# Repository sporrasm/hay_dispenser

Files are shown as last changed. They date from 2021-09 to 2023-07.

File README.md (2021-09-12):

Readme for project horse_feeder

Remeber to run the export script from ESP install dir!

To configure (once per project), run

```
idf.py set-target esp32
idf.py menuconfig
```
Alternatively, WiFi SSID and password can be
set with `wifi_config.sh`. Place SSID and password
in `wifi_info.txt` in the following format:

```
SSID=YOUR_NETWORK_SSID
PASS=YOUR_PASSWORD
```
`wifi_info.txt` is automatically ignored in version
control and thus your password is safe.

To build, run
```
idf.py build
```
Finally, to flash and monitor, run

```
idf.py -p ESP_SERIAL_PORT flash monitor
```

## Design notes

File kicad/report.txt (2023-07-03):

Info: Processing symbol 'R17:Resistor_SMD:R_0805_2012Metric_Pad1.20x1.40mm_HandSolder'.
Info: Processing symbol 'R9:Resistor_SMD:R_0805_2012Metric_Pad1.20x1.40mm_HandSolder'.
Info: Processing symbol 'R10:Resistor_SMD:R_0805_2012Metric_Pad1.20x1.40mm_HandSolder'.
Info: Processing symbol 'R11:Resistor_SMD:R_0805_2012Metric_Pad1.20x1.40mm_HandSolder'.
Info: Processing symbol 'R12:Resistor_SMD:R_0805_2012Metric_Pad1.20x1.40mm_HandSolder'.
Info: Processing symbol 'C1:Capacitor_SMD:C_0805_2012Metric_Pad1.18x1.45mm_HandSolder'.
Info: Processing symbol 'R14:Resistor_SMD:R_0805_2012Metric_Pad1.20x1.40mm_HandSolder'.
Info: Processing symbol 'R15:Resistor_SMD:R_0805_2012Metric_Pad1.20x1.40mm_HandSolder'.
Info: Processing symbol 'R16:Resistor_SMD:R_0805_2012Metric_Pad1.20x1.40mm_HandSolder'.
Info: Processing symbol 'R8:Resistor_SMD:R_0805_2012Metric_Pad1.20x1.40mm_HandSolder'.
Info: Processing symbol 'R18:Resistor_SMD:R_0805_2012Metric_Pad1.20x1.40mm_HandSolder'.
Info: Processing symbol 'R19:Resistor_SMD:R_0805_2012Metric_Pad1.20x1.40mm_HandSolder'.
Info: Processing symbol 'R20:Resistor_SMD:R_0805_2012Metric_Pad1.20x1.40mm_HandSolder'.
Info: Processing symbol 'R21:Resistor_SMD:R_0805_2012Metric_Pad1.20x1.40mm_HandSolder'.
Info: Processing symbol 'R22:Resistor_SMD:R_0805_2012Metric_Pad1.20x1.40mm_HandSolder'.
Info: Processing symbol 'R23:Resistor_SMD:R_0805_2012Metric_Pad1.20x1.40mm_HandSolder'.
Info: Processing symbol 'R24:Resistor_SMD:R_0805_2012Metric_Pad1.20x1.40mm_HandSolder'.
Info: Processing symbol 'R25:Resistor_SMD:R_0805_2012Metric_Pad1.20x1.40mm_HandSolder'.
Info: Processing symbol 'R7:Resistor_SMD:R_0805_2012Metric_Pad1.20x1.40mm_HandSolder'.
Info: Processing symbol 'R6:Resistor_SMD:R_0805_2012Metric_Pad1.20x1.40mm_HandSolder'.
Info: Processing symbol 'R5:Resistor_SMD:R_0805_2012Metric_Pad1.20x1.40mm_HandSolder'.
Info: Processing symbol 'R4:Resistor_SMD:R_0805_2012Metric_Pad1.20x1.40mm_HandSolder'.
Info: Processing symbol 'R3:Resistor_SMD:R_0805_2012Metric_Pad1.20x1.40mm_HandSolder'.
Info: Processing symbol 'R2:Resistor_SMD:R_0805_2012Metric_Pad1.20x1.40mm_HandSolder'.
Info: Processing symbol 'R1:Resistor_SMD:R_0805_2012Metric_Pad1.20x1.40mm_HandSolder'.
Info: Processing symbol 'Q8:Package_TO_SOT_SMD:SOT-23'.
Info: Processing symbol 'Q7:Package_TO_SOT_SMD:SOT-23'.
Info: Processing symbol 'Q6:Package_TO_SOT_SMD:SOT-23'.
Info: Processing symbol 'Q5:Package_TO_SOT_SMD:SOT-23'.
Info: Processing symbol 'Q4:Package_TO_SOT_SMD:SOT-23'.
Info: Processing symbol 'Q3:Package_TO_SOT_SMD:SOT-23'.
Info: Processing symbol 'Q2:Package_TO_SOT_SMD:SOT-23'.
Info: Processing symbol 'Q1:Package_TO_SOT_SMD:SOT-23'.
Info: Processing symbol 'R41:Resistor_SMD:R_0805_2012Metric_Pad1.20x1.40mm_HandSolder'.
Info: Processing symbol 'U9:devkits:AMSROL-783'.
Info: Processing symbol 'U8:devkits:ESP32_DevkitC_ExtraPins'.
Info: Processing symbol 'U6:Package_SO:TSSOP-16_4.4x5mm_P0.65mm'.
Info: Processing symbol 'U5:Package_SO:TSSOP-16_4.4x5mm_P0.65mm'.
Info: Processing symbol 'U4:Package_SO:SOIC-8-1EP_3.9x4.9mm_P1.27mm_EP2.29x3mm'.
Info: Processing symbol 'U3:Package_SO:SOIC-8-1EP_3.9x4.9mm_P1.27mm_EP2.29x3mm'.
Info: Processing symbol 'U2:Package_SO:SOIC-8-1EP_3.9x4.9mm_P1.27mm_EP2.29x3mm'.
Info: Processing symbol 'U1:Package_SO:SOIC-8-1EP_3.9x4.9mm_P1.27mm_EP2.29x3mm'.
Info: Processing symbol 'SW5:Connector_TE-Connectivity:TE_826576-3_1x03_P3.96mm_Vertical'.
Info: Processing symbol 'SW4:Connector_PinHeader_2.54mm:PinHeader_1x02_P2.54mm_Vertical'.
Info: Processing symbol 'SW3:Connector_PinHeader_2.54mm:PinHeader_1x02_P2.54mm_Vertical'.
Info: Processing symbol 'SW2:Connector_PinHeader_2.54mm:PinHeader_1x02_P2.54mm_Vertical'.
Info: Processing symbol 'SW1:Connector_PinHeader_2.54mm:PinHeader_1x02_P2.54mm_Vertical'.
Info: Processing symbol 'Ropt1:Resistor_SMD:R_0805_2012Metric_Pad1.20x1.40mm_HandSolder'.
Info: Processing symbol 'R42:Resistor_SMD:R_0805_2012Metric_Pad1.20x1.40mm_HandSolder'.
Info: Processing symbol 'R13:Resistor_SMD:R_0805_2012Metric_Pad1.20x1.40mm_HandSolder'.
Info: Processing symbol 'R40:Resistor_SMD:R_0805_2012Metric_Pad1.20x1.40mm_HandSolder'.
Info: Processing symbol 'R39:Resistor_SMD:R_0805_2012Metric_Pad1.20x1.40mm_HandSolder'.
Info: Processing symbol 'R38:Resistor_SMD:R_0805_2012Metric_Pad1.20x1.40mm_HandSolder'.
Info: Processing symbol 'R37:Resistor_SMD:R_0805_2012Metric_Pad1.20x1.40mm_HandSolder'.
Info: Processing symbol 'R36:Resistor_SMD:R_0805_2012Metric_Pad1.20x1.40mm_HandSolder'.
Info: Processing symbol 'R35:Resistor_SMD:R_0805_2012Metric_Pad1.20x1.40mm_HandSolder'.
Info: Processing symbol 'R34:Resistor_SMD:R_0805_2012Metric_Pad1.20x1.40mm_HandSolder'.
Info: Processing symbol 'R33:Resistor_SMD:R_0805_2012Metric_Pad1.20x1.40mm_HandSolder'.
Info: Processing symbol 'R32:Resistor_SMD:R_0805_2012Metric_Pad1.20x1.40mm_HandSolder'.
Info: Processing symbol 'R31:Resistor_SMD:R_0805_2012Metric_Pad1.20x1.40mm_HandSolder'.
Info: Processing symbol 'R30:Resistor_SMD:R_0805_2012Metric_Pad1.20x1.40mm_HandSolder'.
Info: Processing symbol 'R29:Resistor_SMD:R_0805_2012Metric_Pad1.20x1.40mm_HandSolder'.
Info: Processing symbol 'R28:Resistor_SMD:R_0805_2012Metric_Pad1.20x1.40mm_HandSolder'.
Info: Processing symbol 'R27:Resistor_SMD:R_0805_2012Metric_Pad1.20x1.40mm_HandSolder'.
Info: Processing symbol 'R26:Resistor_SMD:R_0805_2012Metric_Pad1.20x1.40mm_HandSolder'.
Info: Processing symbol 'D1:Diode_SMD:D_SMB'.
Info: Processing symbol 'J7:Connector_PinHeader_2.54mm:PinHeader_2x02_P2.54mm_Vertical'.
Info: Processing symbol 'J6:Connector_PinHeader_2.54mm:PinHeader_2x02_P2.54mm_Vertical'.
Info: Processing symbol 'J5:Connector_PinHeader_2.54mm:PinHeader_2x02_P2.54mm_Vertical'.
Info: Processing symbol 'J4:Connector_PinHeader_2.54mm:PinHeader_2x02_P2.54mm_Vertical'.
Info: Processing symbol 'J3:Connector_PinHeader_2.54mm:PinHeader_2x02_P2.54mm_Vertical'.
Info: Processing symbol 'J2:Connector_PinHeader_2.54mm:PinHeader_2x02_P2.54mm_Vertical'.
Info: Processing symbol 'J1:Connector_PinHeader_2.54mm:PinHeader_2x02_P2.54mm_Vertical'.
Info: Processing symbol 'D8:Diode_SMD:D_SMB'.
Info: Processing symbol 'D7:Diode_SMD:D_SMB'.
Info: Processing symbol 'D6:Diode_SMD:D_SMB'.
Info: Processing symbol 'D5:Diode_SMD:D_SMB'.
Info: Processing symbol 'D4:Diode_SMD:D_SMB'.
Info: Processing symbol 'D3:Diode_SMD:D_SMB'.
Info: Processing symbol 'D2:Diode_SMD:D_SMB'.
Info: Processing symbol 'L2:Inductor_THT:L_Radial_D7.0mm_P3.00mm'.
Info: Processing symbol 'C14:Capacitor_THT:CP_Radial_D5.0mm_P2.50mm'.
Info: Processing symbol 'C13:Capacitor_THT:CP_Radial_D5.0mm_P2.50mm'.
Info: Processing symbol 'C12:Capacitor_THT:CP_Radial_D8.0mm_P3.50mm'.
Info: Processing symbol 'C11:Capacitor_THT:CP_Radial_D5.0mm_P2.50mm'.
Info: Processing symbol 'C10:Capacitor_THT:CP_Radial_D5.0mm_P2.50mm'.
Info: Processing symbol 'C9:Capacitor_THT:CP_Radial_D8.0mm_P3.50mm'.
Info: Processing symbol 'C8:Capacitor_SMD:C_0805_2012Metric_Pad1.18x1.45mm_HandSolder'.
Info: Processing symbol 'C7:Capacitor_SMD:C_0805_2012Metric_Pad1.18x1.45mm_HandSolder'.
Info: Processing symbol 'C6:Capacitor_SMD:C_0805_2012Metric_Pad1.18x1.45mm_HandSolder'.
Info: Processing symbol 'C5:Capacitor_SMD:C_0805_2012Metric_Pad1.18x1.45mm_HandSolder'.
Info: Processing symbol 'C4:Capacitor_SMD:C_0805_2012Metric_Pad1.18x1.45mm_HandSolder'.
Info: Processing symbol 'C3:Capacitor_SMD:C_0805_2012Metric_Pad1.18x1.45mm_HandSolder'.
Info: Processing symbol 'C2:Capacitor_SMD:C_0805_2012Metric_Pad1.18x1.45mm_HandSolder'.
Info: Processing symbol 'L3:Inductor_THT:L_Radial_D7.0mm_P3.00mm'.
Info: Processing symbol 'L1:Inductor_THT:L_Radial_D7.0mm_P3.00mm'.
Info: Processing symbol 'J9:Connector_Phoenix_MSTB:PhoenixContact_MSTBA_2,5_2-G_1x02_P5.00mm_Horizontal'.
Info: Processing symbol 'J10:Connector_PinHeader_2.00mm:PinHeader_1x04_P2.00mm_Vertical'.
Info: Processing symbol 'J8:Connector_PinHeader_2.54mm:PinHeader_2x02_P2.54mm_Vertical'.
Updated D5 symbol association from /00000000-0000-0000-0000-000061ebca90/00000000-0000-0000-0000-000061f9a212 to /00000000-0000-0000-0000-000061ebca90/12310255-a125-40a2-8815-03da1e133a0b.
Reconnected Q5 pin 1 from Net-(Q1-G) to Net-(Q5-G).
Reconnected J8 pin 4 from /IOs/LOCK_DET1 to /IOs/LOCK_DET7.
Reconnected D4 pin 2 from Net-(D2-A) to Net-(D4-A).
Updated D4 symbol association from /00000000-0000-0000-0000-000061ebca90/1fadecef-52da-4aaa-b496-044390b111f7 to /00000000-0000-0000-0000-000061ebca90/f83071ec-e386-489c-af28-ea3d26ad8b88.
Reconnected Q6 pin 3 from Net-(D2-A) to Net-(D6-A).
Reconnected D3 pin 2 from Net-(D1-A) to Net-(D3-A).
Updated D3 symbol association from /00000000-0000-0000-0000-000061ebca90/00000000-0000-0000-0000-000061f9a212 to /00000000-0000-0000-0000-000061ebca90/ba43a25b-48b8-4457-9719-1656a0430705.
Reconnected Q6 pin 1 from Net-(Q2-G) to Net-(Q6-G).
Updated Q6 symbol association from /00000000-0000-0000-0000-000061ebca90/9a64ff62-3964-40c4-85d5-2005a53f7bb7 to /00000000-0000-0000-0000-000061ebca90/19cce44a-ca22-4e9a-8f8b-97bd614c21f1.
Reconnected J8 pin 3 from Net-(D2-A) to Net-(D8-A).
Reconnected Q5 pin 3 from Net-(D1-A) to Net-(D5-A).
Updated R29 symbol association from /00000000-0000-0000-0000-000061ebca90/00000000-0000-0000-0000-000061f8473e to /00000000-0000-0000-0000-000061ebca90/3bc0eca3-92dc-4e1d-8b31-45b180863d8f.
Reconnected D5 pin 2 from Net-(D1-A) to Net-(D5-A).
Reconnected R32 pin 1 from /IOs/LOCK_EN0 to /IOs/LOCK_EN6.
Reconnected R32 pin 2 from Net-(U1-ENB) to Net-(U4-ENB).
Updated R32 symbol association from /00000000-0000-0000-0000-000061ebca90/00000000-0000-0000-0000-000061f84748 to /00000000-0000-0000-0000-000061ebca90/12d70f20-32db-4ce9-8402-37e04de7cd11.
Updated Q7 symbol association from /00000000-0000-0000-0000-000061ebca90/00000000-0000-0000-0000-000061f9a22a to /00000000-0000-0000-0000-000061ebca90/117ebf1d-a23b-43cb-92d2-cf0df6883d6a.
Reconnected R31 pin 1 from Net-(U1-ENA) to Net-(U4-ENA).
Reconnected R31 pin 2 from /IOs/LOCK_EN1 to /IOs/LOCK_EN7.
Updated R31 symbol association from /00000000-0000-0000-0000-000061ebca90/00000000-0000-0000-0000-000061f8473e to /00000000-0000-0000-0000-000061ebca90/c096ada7-25bf-42d8-b60a-c3b1d2fc6672.
Updated D6 symbol association from /00000000-0000-0000-0000-000061ebca90/1fadecef-52da-4aaa-b496-044390b111f7 to /00000000-0000-0000-0000-000061ebca90/009bf2af-9f41-490d-a20b-dce77ff50deb.
Reconnected R30 pin 2 from Net-(U1-ENB) to Net-(U3-ENB).
Reconnected R30 pin 1 from /IOs/LOCK_EN0 to /IOs/LOCK_EN4.
Updated R30 symbol association from /00000000-0000-0000-0000-000061ebca90/00000000-0000-0000-0000-000061f84748 to /00000000-0000-0000-0000-000061ebca90/f51487ca-ee80-4a78-abcf-102a507cea02.
Reconnected D6 pin 2 from Net-(D2-A) to Net-(D6-A).
Reconnected R29 pin 2 from /IOs/LOCK_EN1 to /IOs/LOCK_EN5.
Reconnected R29 pin 1 from Net-(U1-ENA) to Net-(U3-ENA).
Reconnected J7 pin 4 from /IOs/LOCK_DET0 to /IOs/LOCK_DET6.
Reconnected U3 pin 4 from /IOs/LOCK_IN1 to /IOs/LOCK_IN5.
Updated Q3 symbol association from /00000000-0000-0000-0000-000061ebca90/00000000-0000-0000-0000-000061f9a22a to /00000000-0000-0000-0000-000061ebca90/dab6c745-e6cc-45fe-9a9b-13cf7740417a.
Reconnected Q3 pin 1 from Net-(Q1-G) to Net-(Q3-G).
Reconnected U4 pin 1 from Net-(U1-ENA) to Net-(U4-ENA).
Reconnected U4 pin 2 from /IOs/LOCK_IN0 to /IOs/LOCK_IN6.
Reconnected U4 pin 4 from /IOs/LOCK_IN1 to /IOs/LOCK_IN7.
Reconnected U4 pin 5 from /IOs/LOCK1 to /IOs/LOCK7.
Reconnected U4 pin 7 from /IOs/LOCK0 to /IOs/LOCK6.
Reconnected U4 pin 8 from Net-(U1-ENB) to Net-(U4-ENB).
Updated U4 symbol association from /00000000-0000-0000-0000-000061ebca90/00000000-0000-0000-0000-000061fc2397 to /00000000-0000-0000-0000-000061ebca90/329a1e8b-e309-4d9a-a68a-94c8a32ff173.
Reconnected Q3 pin 3 from Net-(D1-A) to Net-(D3-A).
Reconnected U3 pin 8 from Net-(U1-ENB) to Net-(U3-ENB).
Reconnected U3 pin 7 from /IOs/LOCK0 to /IOs/LOCK4.
Reconnected U3 pin 5 from /IOs/LOCK1 to /IOs/LOCK5.
Updated Q5 symbol association from /00000000-0000-0000-0000-000061ebca90/00000000-0000-0000-0000-000061f9a22a to /00000000-0000-0000-0000-000061ebca90/90347d65-daa5-4414-a60e-72c4a4d0bfb0.
Reconnected U3 pin 2 from /IOs/LOCK_IN0 to /IOs/LOCK_IN4.
Reconnected U3 pin 1 from Net-(U1-ENA) to Net-(U3-ENA).
Updated U3 symbol association from /00000000-0000-0000-0000-000061ebca90/00000000-0000-0000-0000-000061fc2397 to /00000000-0000-0000-0000-000061ebca90/f14f373f-7c34-4b97-81f3-ad92c1f3f635.
Reconnected U2 pin 8 from Net-(U1-ENB) to Net-(U2-ENB).
Reconnected U2 pin 7 from /IOs/LOCK0 to /IOs/LOCK2.
Reconnected U2 pin 5 from /IOs/LOCK1 to /IOs/LOCK3.
Reconnected U2 pin 4 from /IOs/LOCK_IN1 to /IOs/LOCK_IN3.
Reconnected U2 pin 2 from /IOs/LOCK_IN0 to /IOs/LOCK_IN2.
Reconnected U2 pin 1 from Net-(U1-ENA) to Net-(U2-ENA).
Updated U2 symbol association from /00000000-0000-0000-0000-000061ebca90/00000000-0000-0000-0000-000061fc2397 to /00000000-0000-0000-0000-000061ebca90/1f8c6d32-524a-4a61-9146-b464a2e4b00f.
Updated Q4 symbol association from /00000000-0000-0000-0000-000061ebca90/9a64ff62-3964-40c4-85d5-2005a53f7bb7 to /00000000-0000-0000-0000-000061ebca90/2e4807ac-fbeb-4c4a-b1f8-ade59b8256ed.
Reconnected Q4 pin 1 from Net-(Q2-G) to Net-(Q4-G).
Reconnected Q4 pin 3 from Net-(D2-A) to Net-(D4-A).
Reconnected R10 pin 2 from /IOs/LOCK1 to /IOs/LOCK3.
Reconnected R15 pin 1 from /IOs/LOCK_DET0 to /IOs/LOCK_DET4.
Updated R15 symbol association from /00000000-0000-0000-0000-000061ebca90/00000000-0000-0000-0000-000061f9a118 to /00000000-0000-0000-0000-000061ebca90/5d248cbb-a3ee-4746-98de-e42f1b14ef73.
Reconnected J4 pin 3 from Net-(D2-A) to Net-(D4-A).
Reconnected R14 pin 1 from Net-(Q1-G) to Net-(Q5-G).
Updated R14 symbol association from /00000000-0000-0000-0000-000061ebca90/00000000-0000-0000-0000-000061f9a127 to /00000000-0000-0000-0000-000061ebca90/5689a1f5-9090-4234-bba9-7dff9da78761.
Reconnected Q7 pin 3 from Net-(D1-A) to Net-(D7-A).
Reconnected R13 pin 1 from Net-(Q1-G) to Net-(Q5-G).
Reconnected R13 pin 2 from /IOs/LOCK0 to /IOs/LOCK4.
Updated R13 symbol association from /00000000-0000-0000-0000-000061ebca90/00000000-0000-0000-0000-000061f9a12d to /00000000-0000-0000-0000-000061ebca90/e7271d92-2a59-4a4c-9ece-0f144f666454.
Reconnected R12 pin 1 from /IOs/LOCK_DET1 to /IOs/LOCK_DET3.
Updated R12 symbol association from /00000000-0000-0000-0000-000061ebca90/acf82a41-7d0e-472a-a831-509c7dad960c to /00000000-0000-0000-0000-000061ebca90/bc75ee53-f973-43e8-9b8a-a9dcb3717276.
Updated J5 symbol association from /00000000-0000-0000-0000-000061ebca90/00000000-0000-0000-0000-000061f9a109 to /00000000-0000-0000-0000-000061ebca90/01534e29-1c65-493a-a183-ee503e500c0f.
Reconnected R11 pin 1 from Net-(Q2-G) to Net-(Q4-G).
Updated R11 symbol association from /00000000-0000-0000-0000-000061ebca90/e005b53f-12e7-4917-b024-14621842eea1 to /00000000-0000-0000-0000-000061ebca90/f1c19577-37a0-416f-b9f6-60572b592bf5.
Reconnected J5 pin 3 from Net-(D1-A) to Net-(D5-A).
Reconnected J4 pin 4 from /IOs/LOCK_DET1 to /IOs/LOCK_DET3.
Reconnected R10 pin 1 from Net-(Q2-G) to Net-(Q4-G).
Updated R10 symbol association from /00000000-0000-0000-0000-000061ebca90/a2109c77-97ea-4bdb-9450-69fe4743dba1 to /00000000-0000-0000-0000-000061ebca90/110e5a1b-0579-4342-8a50-bc9ee74117f4.
Reconnected J5 pin 4 from /IOs/LOCK_DET0 to /IOs/LOCK_DET4.
Reconnected R9 pin 1 from /IOs/LOCK_DET0 to /IOs/LOCK_DET2.
Updated R9 symbol association from /00000000-0000-0000-0000-000061ebca90/00000000-0000-0000-0000-000061f9a118 to /00000000-0000-0000-0000-000061ebca90/a2a08252-e1a3-4e8e-a624-c2db73924c49.
Reconnected J7 pin 3 from Net-(D1-A) to Net-(D7-A).
Reconnected R8 pin 1 from Net-(Q1-G) to Net-(Q3-G).
Updated R8 symbol association from /00000000-0000-0000-0000-000061ebca90/00000000-0000-0000-0000-000061f9a127 to /00000000-0000-0000-0000-000061ebca90/5699d61c-54a2-4d67-a252-4f0f22aa03cb.
Updated J6 symbol association from /00000000-0000-0000-0000-000061ebca90/d37b7b18-48a2-43dd-b725-8d8200de3ad7 to /00000000-0000-0000-0000-000061ebca90/7799ac4f-bc16-4e58-80f5-ee678a479432.
Reconnected R7 pin 1 from Net-(Q1-G) to Net-(Q3-G).
Reconnected R7 pin 2 from /IOs/LOCK0 to /IOs/LOCK2.
Updated R7 symbol association from /00000000-0000-0000-0000-000061ebca90/00000000-0000-0000-0000-000061f9a12d to /00000000-0000-0000-0000-000061ebca90/1e97676b-6e90-4e2b-9f52-2bc77df03034.
Reconnected J6 pin 3 from Net-(D2-A) to Net-(D6-A).
Reconnected J6 pin 4 from /IOs/LOCK_DET1 to /IOs/LOCK_DET5.
Updated J7 symbol association from /00000000-0000-0000-0000-000061ebca90/00000000-0000-0000-0000-000061f9a109 to /00000000-0000-0000-0000-000061ebca90/1b84dabf-0c1a-4e32-9baa-dc91dcef677a.
Updated J8 symbol association from /00000000-0000-0000-0000-000061ebca90/d37b7b18-48a2-43dd-b725-8d8200de3ad7 to /00000000-0000-0000-0000-000061ebca90/7a27e839-1899-4622-9983-cdac9ac2dc0d.
Reconnected R28 pin 1 from /IOs/LOCK_EN0 to /IOs/LOCK_EN2.
Updated R28 symbol association from /00000000-0000-0000-0000-000061ebca90/00000000-0000-0000-0000-000061f84748 to /00000000-0000-0000-0000-000061ebca90/9e823606-f83d-4ab2-8a34-e646199f153e.
Updated D7 symbol association from /00000000-0000-0000-0000-000061ebca90/00000000-0000-0000-0000-000061f9a212 to /00000000-0000-0000-0000-000061ebca90/b1030530-6fb9-4591-98a9-0427e75660df.
Reconnected R27 pin 2 from /IOs/LOCK_EN1 to /IOs/LOCK_EN3.
Reconnected R27 pin 1 from Net-(U1-ENA) to Net-(U2-ENA).
Updated R27 symbol association from /00000000-0000-0000-0000-000061ebca90/00000000-0000-0000-0000-000061f8473e to /00000000-0000-0000-0000-000061ebca90/26a5f1ab-7ebe-4985-b59a-fd3232592324.
Reconnected D7 pin 2 from Net-(D1-A) to Net-(D7-A).
Reconnected R28 pin 2 from Net-(U1-ENB) to Net-(U2-ENB).
Reconnected Q7 pin 1 from Net-(Q1-G) to Net-(Q7-G).
Updated D8 symbol association from /00000000-0000-0000-0000-000061ebca90/1fadecef-52da-4aaa-b496-044390b111f7 to /00000000-0000-0000-0000-000061ebca90/9ebdfd22-79c4-4adf-85de-91e1239ecd49.
Reconnected D8 pin 2 from Net-(D2-A) to Net-(D8-A).
Updated Q8 symbol association from /00000000-0000-0000-0000-000061ebca90/9a64ff62-3964-40c4-85d5-2005a53f7bb7 to /00000000-0000-0000-0000-000061ebca90/89a83a01-4313-41c3-ab5b-a217104dbb12.
Reconnected Q8 pin 3 from Net-(D2-A) to Net-(D8-A).
Updated J4 symbol association from /00000000-0000-0000-0000-000061ebca90/d37b7b18-48a2-43dd-b725-8d8200de3ad7 to /00000000-0000-0000-0000-000061ebca90/230b0a54-814c-4633-86d4-6288c8a4b25b.
Reconnected R17 pin 1 from Net-(Q2-G) to Net-(Q6-G).
Updated R16 symbol association from /00000000-0000-0000-0000-000061ebca90/a2109c77-97ea-4bdb-9450-69fe4743dba1 to /00000000-0000-0000-0000-000061ebca90/7600460e-baca-4eef-a013-d1cb4ffcadad.
Reconnected R16 pin 1 from Net-(Q2-G) to Net-(Q6-G).
Reconnected R16 pin 2 from /IOs/LOCK1 to /IOs/LOCK5.
Reconnected Q8 pin 1 from Net-(Q2-G) to Net-(Q8-G).
Updated R17 symbol association from /00000000-0000-0000-0000-000061ebca90/e005b53f-12e7-4917-b024-14621842eea1 to /00000000-0000-0000-0000-000061ebca90/eb4bc25c-40cd-4988-a59e-3364879d56c7.
Reconnected J3 pin 4 from /IOs/LOCK_DET0 to /IOs/LOCK_DET2.
Updated R18 symbol association from /00000000-0000-0000-0000-000061ebca90/acf82a41-7d0e-472a-a831-509c7dad960c to /00000000-0000-0000-0000-000061ebca90/407302c0-80a5-49a3-b481-c82105730bca.
Reconnected R18 pin 1 from /IOs/LOCK_DET1 to /IOs/LOCK_DET5.
Reconnected J3 pin 3 from Net-(D1-A) to Net-(D3-A).
Updated J3 symbol association from /00000000-0000-0000-0000-000061ebca90/00000000-0000-0000-0000-000061f9a109 to /00000000-0000-0000-0000-000061ebca90/5bc772af-2207-48a7-a277-9bfb6a1bbd47.
Warning: No net found for symbol U8 pin 40.
Warning: No net found for symbol U2 pin 9.
Warning: No net found for symbol U5 pin 10.
Warning: No net found for symbol U4 pin 9.
Warning: No net found for symbol U8 pin 39.
Warning: No net found for symbol U6 pin 10.
Warning: No net found for symbol U1 pin 9.
Warning: No net found for symbol U4 pin 9.
Warning: No net found for symbol U2 pin 9.
Warning: No net found for symbol U3 pin 9.
Warning: No net found for symbol U3 pin 9.
Error: Multiple footprints found for 'R29'.
Error: Multiple footprints found for 'R28'.
Error: Multiple footprints found for 'U4'.
Error: Multiple footprints found for 'R27'.
Error: Multiple footprints found for 'R30'.
Error: Multiple footprints found for 'U3'.
Error: Multiple footprints found for 'R31'.
Error: Multiple footprints found for 'R32'.
Error: Multiple footprints found for 'U2'.

Info: Total warnings: 11, errors: 9.

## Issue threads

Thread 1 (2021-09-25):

Timer fires too soon if alarm time is large

sporrasm, 2021-09-25:

sporrasm, 2021-09-25:
The timer seems to fire too soon provided that the value to be set is too large. This may be due to the fact the the timer alarm value is given in TIMER_SCALE units, which is equal to APB_CLOCK / CLOCK_DIV. Need to perform check whether the integer overflows and causes this.

sporrasm, 2021-09-25:
Fixed by a65deb02. Seems to be that I forgot to cast the input time in seconds to uint64_t, causing the alarm time value to be garbage. Hence, timer was acting erratically.

Closed 2021-09-25.

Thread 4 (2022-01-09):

Triggering locks after power down

sporrasm, 2022-01-09:
If power down happens during the feeding routine, the next lock corresponding to the next time stamp is released. This may cause issues if one of the plates has not triggered during the power down. Solution is to pulse all locks that are before the next lock to be pulsed (or monitor lock state via hardware)

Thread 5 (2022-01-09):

Timezone settings

sporrasm, 2022-01-09:
Timer is off by one hour during DST. Need to fix this at some point

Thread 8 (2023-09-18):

Change pin order of I2C io expanders

sporrasm, 2023-09-18:
The pin order in PCB rev 1.2 is a bit wonky for the I2C expanders. Could worth to change them to correct order so that lock index 0 truly corresponds to index 0 etc.

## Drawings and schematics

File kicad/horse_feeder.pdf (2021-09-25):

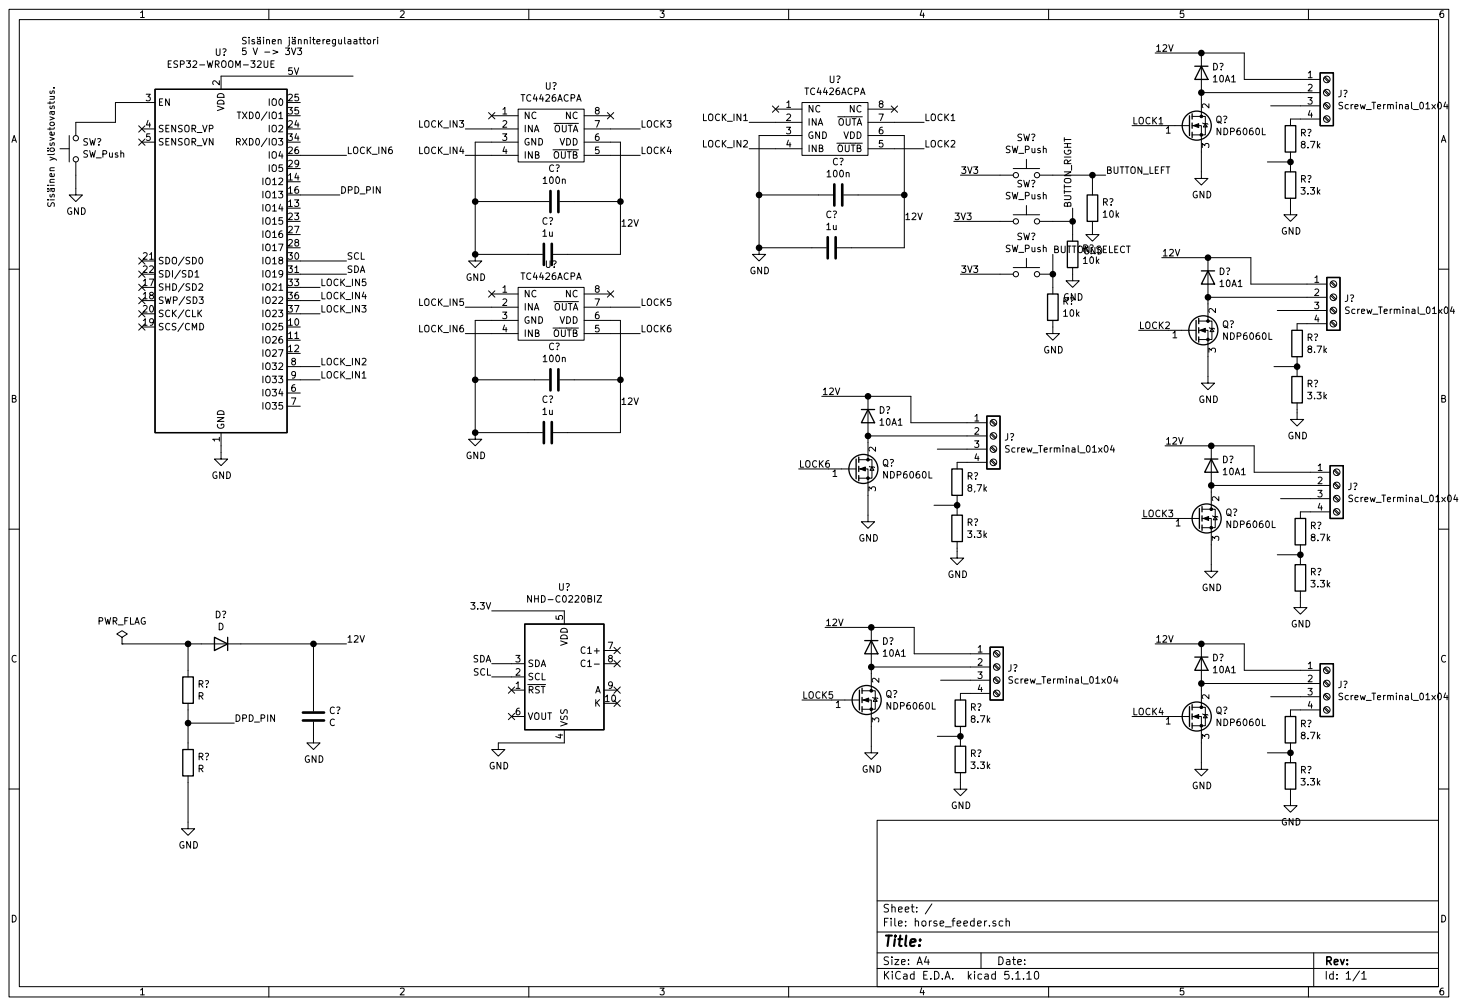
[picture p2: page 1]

LOCK1 Sisäinen jänniteregulaattori 5 V -> 3V3 Sisäinen ylösvetovastus.

2 SCK/CLK 20 SDO/SD0 21 SDI/SD1 22

File: horse_feeder.sch Sheet: / GND

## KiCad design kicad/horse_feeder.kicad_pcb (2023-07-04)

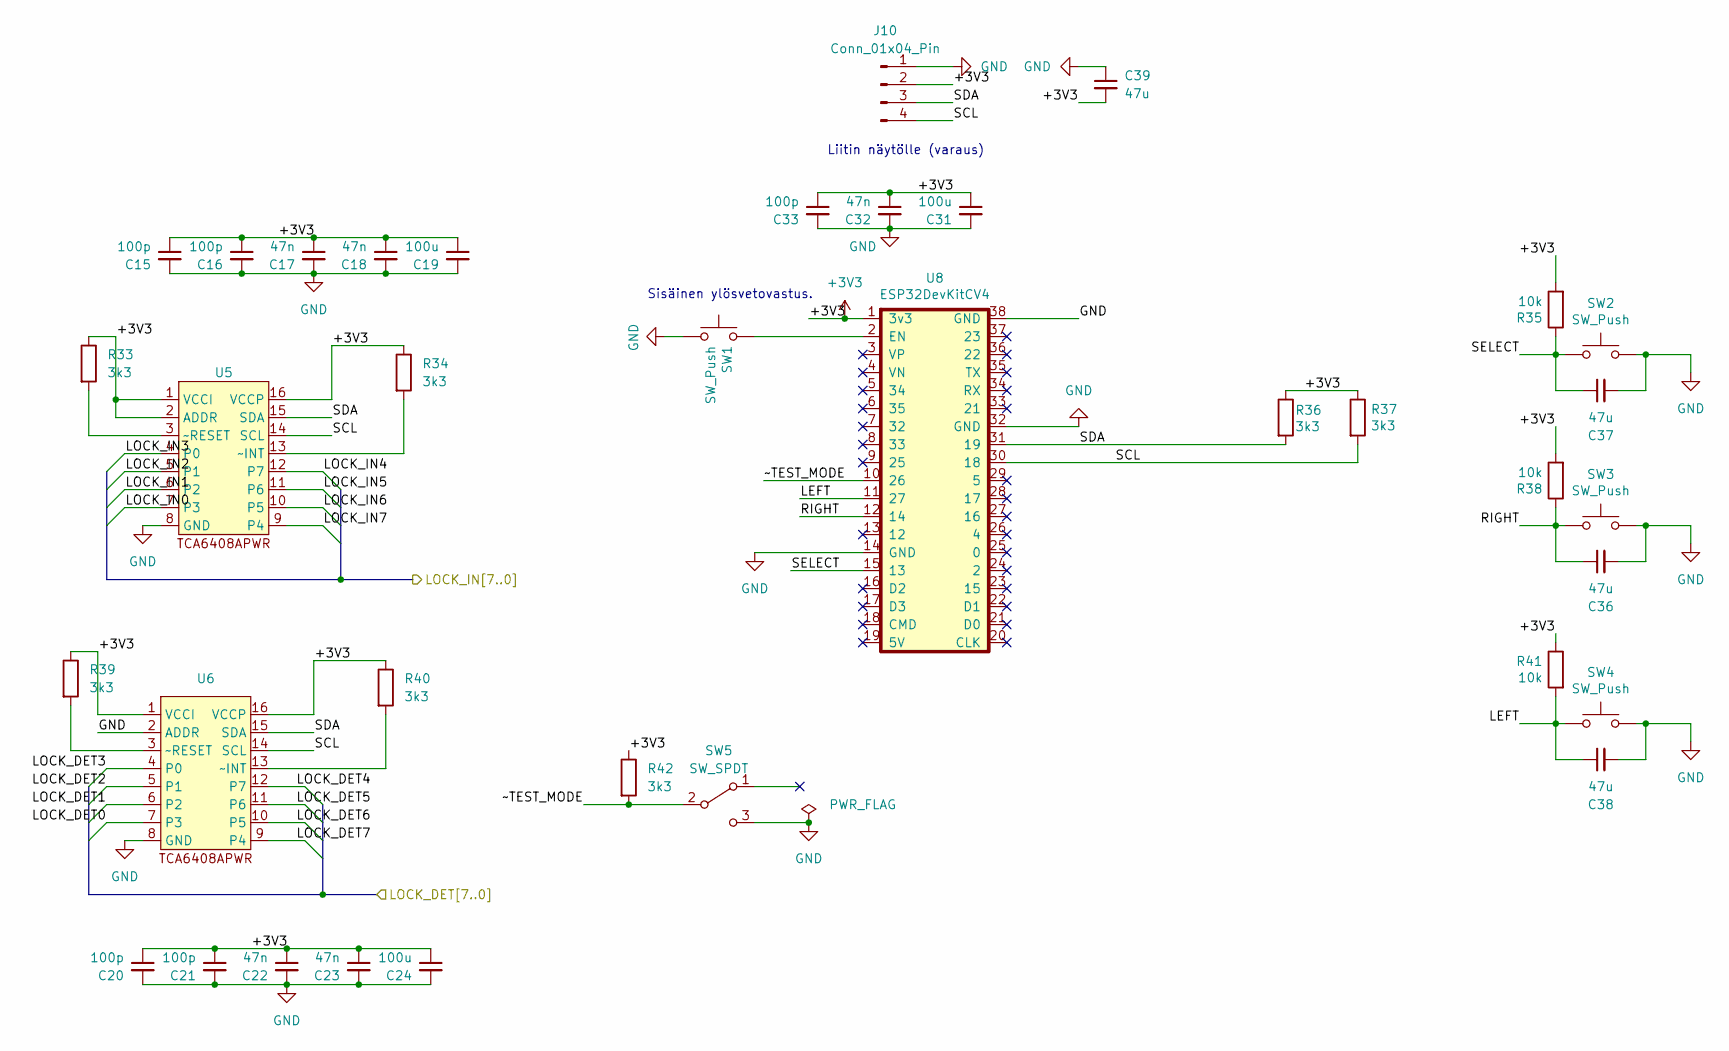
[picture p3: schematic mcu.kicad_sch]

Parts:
C15, C16, C20, C21, C33: 100p; C_0805_2012Metric_Pad1.18x1.45mm_HandSolder
C17, C18, C22, C23, C32: 47n; C_0805_2012Metric_Pad1.18x1.45mm_HandSolder
C19, C24, C31: 100u; CP_Radial_D5.0mm_P2.50mm
C36, C37, C38, C39: 47u; C_0805_2012Metric_Pad1.18x1.45mm_HandSolder
J10: Conn_01x04_Pin; PinHeader_1x04_P2.00mm_Vertical
R33, R34, R36, R37, R39, R40, R42: 3k3; R_0805_2012Metric_Pad1.20x1.40mm_HandSolder
R35, R38, R41: 10k; R_0805_2012Metric_Pad1.20x1.40mm_HandSolder
SW1, SW2, SW3, SW4: SW_Push; PinHeader_1x02_P2.54mm_Vertical
SW5: SW_SPDT; TE_826576-3_1x03_P3.96mm_Vertical
U5, U6: TSSOP-16_4.4x5mm_P0.65mm
U8: ESP32DevKitCV4; ESP32-DevkitC

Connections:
+3V3: C15.1, C16.1, C17.1, C18.1, C19.1, C20.1, C21.1, C22.1, C23.1, C24.1, C31.1, C32.1, C33.1, C39.2, J10.2, R33.1, R34.1, R35.2, R36.1, R37.1, R38.2, R39.1, R40.1, R41.1, R42.1, U5.1 (VCCI), U5.2 (ADDR), U5.16 (VCCP), U6.1 (VCCI), U6.16 (VCCP), U8.1 (3v3); also elsewhere on the board
/IOS/LOCK_DET0: U6.7 (P3); also elsewhere on the board
/IOS/LOCK_DET1: U6.6 (P2); also elsewhere on the board
/IOS/LOCK_DET2: U6.5 (P1); also elsewhere on the board
/IOS/LOCK_DET3: U6.4 (P0); also elsewhere on the board
/IOS/LOCK_DET4: U6.12 (P7); also elsewhere on the board
/IOS/LOCK_DET5: U6.11 (P6); also elsewhere on the board
/IOS/LOCK_DET6: U6.10 (P5); also elsewhere on the board
/IOS/LOCK_DET7: U6.9 (P4); also elsewhere on the board
/IOS/LOCK_IN0: U5.7 (P3); also elsewhere on the board
/IOS/LOCK_IN1: U5.6 (P2); also elsewhere on the board
/IOS/LOCK_IN2: U5.5 (P1); also elsewhere on the board
/IOS/LOCK_IN3: U5.4 (P0); also elsewhere on the board
/IOS/LOCK_IN4: U5.12 (P7); also elsewhere on the board
/IOS/LOCK_IN5: U5.11 (P6); also elsewhere on the board
/IOS/LOCK_IN6: U5.10 (P5); also elsewhere on the board
/IOS/LOCK_IN7: U5.9 (P4); also elsewhere on the board
/MCU/LEFT: C38.1, R41.2, SW4.2, U8.11 (27)
/MCU/RIGHT: C36.1, R38.1, SW3.2, U8.12 (14)
/MCU/SCL: J10.4, R37.2, U5.14 (SCL), U6.14 (SCL), U8.30 (18)
/MCU/SDA: J10.3, R36.2, U5.15 (SDA), U6.15 (SDA), U8.31 (19)
/MCU/SELECT: C37.1, R35.1, SW2.2, U8.15 (13)
/MCU/~TEST_MODE: R42.2, SW5.2 (B), U8.10 (26)
GND: C15.2, C16.2, C17.2, C18.2, C19.2, C20.2, C21.2, C22.2, C23.2, C24.2, C31.2, C32.2, C33.2, C36.2, C37.2, C38.2, C39.1, J10.1, SW1.1, SW2.1, SW3.1, SW4.1, SW5.3 (C), U5.8 (GND), U6.2 (ADDR), U6.8 (GND), U8.14 (GND), U8.32 (GND), U8.38 (GND); also elsewhere on the board
unnamed: R34.2, U5.13 (~INT)
unnamed: R33.2, U5.3 (~RESET)
unnamed: R40.2, U6.13 (~INT)
unnamed: R39.2, U6.3 (~RESET)
unnamed: SW1.2, U8.2 (EN)

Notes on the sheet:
Sisäinen ylösvetovastus.
Liitin näytölle (varaus)

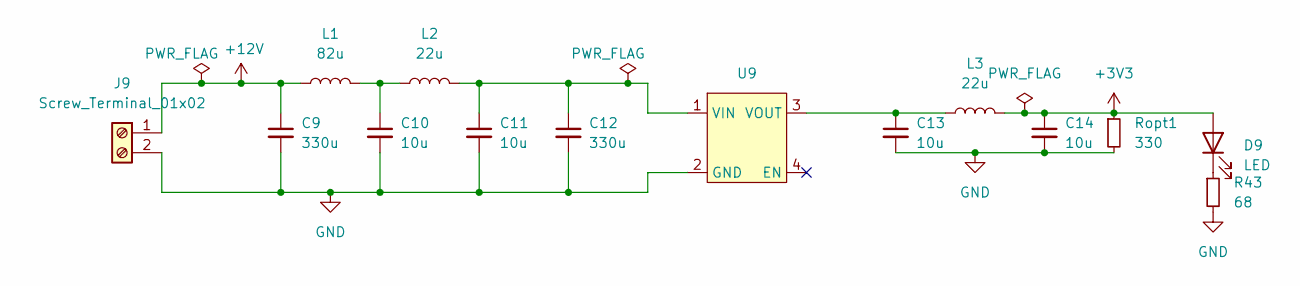
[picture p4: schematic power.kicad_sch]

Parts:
C9, C12: 330u; CP_Radial_D8.0mm_P3.50mm
C10, C11, C13, C14: 10u; CP_Radial_D5.0mm_P2.50mm
D9: LED; LED_PLCC-2_3x2mm_KA
J9: Screw_Terminal_01x02; PhoenixContact_MSTBA_2,5_2-G_1x02_P5.00mm_Horizontal
L1: 82u; L_Radial_D7.0mm_P3.00mm
L2, L3: 22u; L_Radial_D7.0mm_P3.00mm
R43: 68; R_0805_2012Metric_Pad1.20x1.40mm_HandSolder
Ropt1: 330; R_0805_2012Metric_Pad1.20x1.40mm_HandSolder
U9: AMSROL-783

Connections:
+3V3: C14.1, D9.2 (A), L3.2, Ropt1.1; also elsewhere on the board
+12V: C9.1, J9.1, L1.1; also elsewhere on the board
GND: C9.2, C10.2, C11.2, C12.2, C13.2, C14.2, J9.2, R43.2, Ropt1.2, U9.2 (GND); also elsewhere on the board
unnamed: C10.1, L1.2, L2.1
unnamed 50: D9.1 (K), R43.1; also elsewhere on the board
unnamed: C11.1, C12.1, L2.2, U9.1 (VIN)
unnamed: C13.1, L3.1, U9.3 (VOUT)

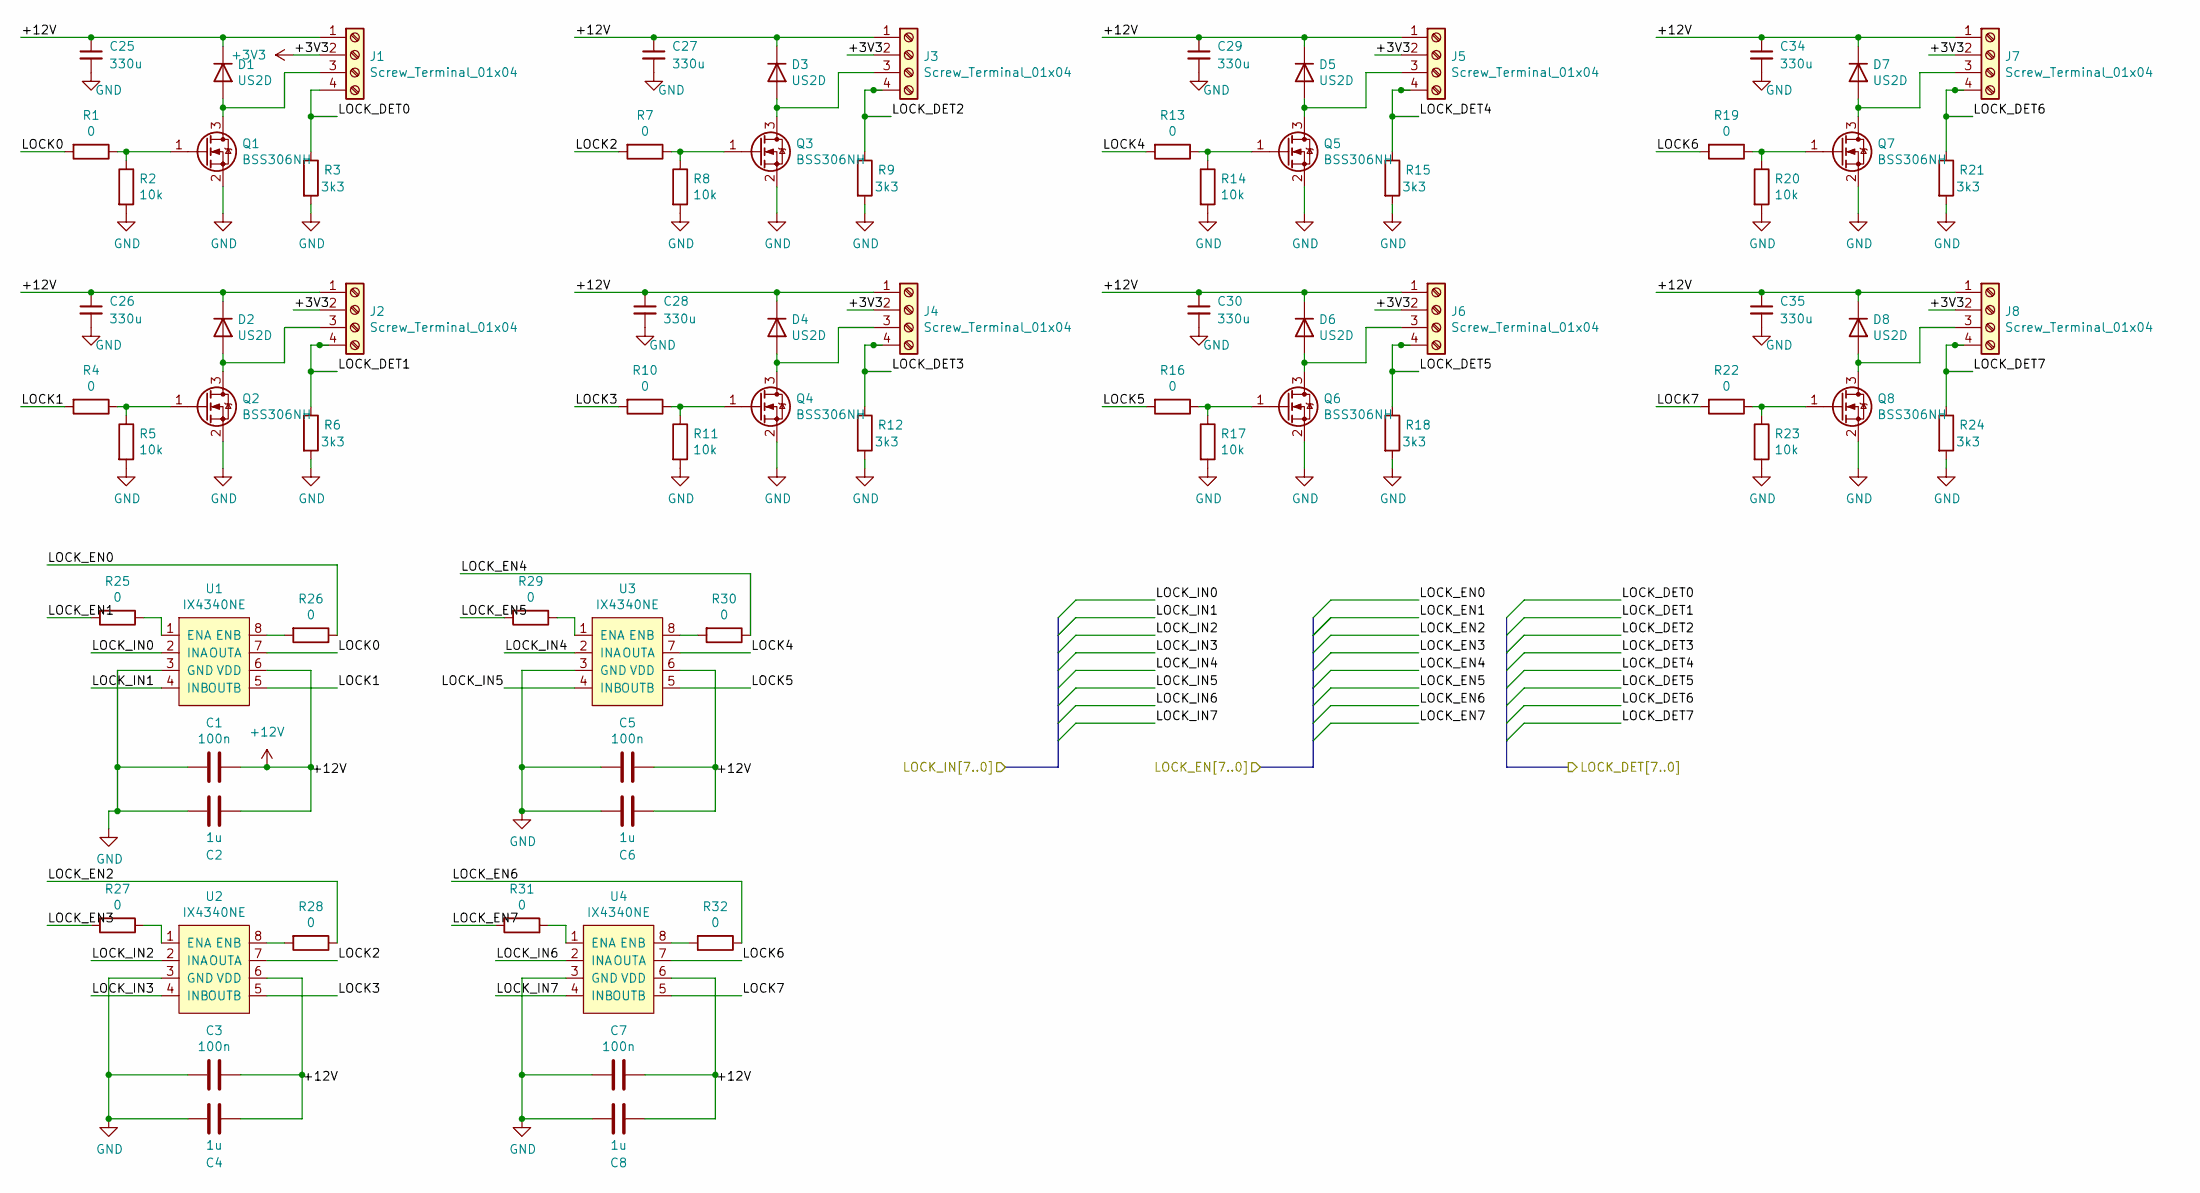
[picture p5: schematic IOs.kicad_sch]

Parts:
C1, C3, C5, C7: 100n; C_0805_2012Metric_Pad1.18x1.45mm_HandSolder
C2, C4, C6, C8: 1u; C_0805_2012Metric_Pad1.18x1.45mm_HandSolder
C25, C26, C27, C28, C29, C30, C34, C35: 330u; CP_Radial_D8.0mm_P3.50mm
D1, D2, D3, D4, D5, D6, D7, D8: US2D; D_SMB
J1, J2, J3, J4, J5, J6, J7, J8: Screw_Terminal_01x04; PinHeader_2x02_P2.54mm_Vertical
Q1, Q2, Q3, Q4, Q5, Q6, Q7, Q8: BSS306NH; SOT-23
R1, R4, R7, R10, R13, R16, R19, R22, R25, R26, R27, R28, R29, R30, R31, R32: 0; R_0805_2012Metric_Pad1.20x1.40mm_HandSolder
R2, R5, R8, R11, R14, R17, R20, R23: 10k; R_0805_2012Metric_Pad1.20x1.40mm_HandSolder
R3, R6, R9, R12, R15, R18, R21, R24: 3k3; R_0805_2012Metric_Pad1.20x1.40mm_HandSolder
U1, U2, U3, U4: IX4340NE; SOIC-8-1EP_3.9x4.9mm_P1.27mm_EP2.29x3mm

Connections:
+3V3: J1.2, J2.2, J3.2, J4.2, J5.2, J6.2, J7.2, J8.2; also elsewhere on the board
+12V: C1.1, C2.1, C3.1, C4.1, C5.1, C6.1, C7.1, C8.1, C25.1, C26.1, C27.1, C28.1, C29.1, C30.1, C34.1, C35.1, D1.1 (K), D2.1 (K), D3.1 (K), D4.1 (K), D5.1 (K), D6.1 (K), D7.1 (K), D8.1 (K), J1.1, J2.1, J3.1, J4.1, J5.1, J6.1, J7.1, J8.1, U1.6 (VDD), U2.6 (VDD), U3.6 (VDD), U4.6 (VDD); also elsewhere on the board
/IOS/LOCK0: R1.2, U1.7 (OUTA)
/IOS/LOCK1: R4.2, U1.5 (OUTB)
/IOS/LOCK2: R7.2, U2.7 (OUTA)
/IOS/LOCK3: R10.2, U2.5 (OUTB)
/IOS/LOCK4: R13.2, U3.7 (OUTA)
/IOS/LOCK5: R16.2, U3.5 (OUTB)
/IOS/LOCK6: R19.2, U4.7 (OUTA)
/IOS/LOCK7: R22.2, U4.5 (OUTB)
/IOS/LOCK_DET0: J1.4, R3.1; also elsewhere on the board
/IOS/LOCK_DET1: J2.4, R6.1; also elsewhere on the board
/IOS/LOCK_DET2: J3.4, R9.1; also elsewhere on the board
/IOS/LOCK_DET3: J4.4, R12.1; also elsewhere on the board
/IOS/LOCK_DET4: J5.4, R15.1; also elsewhere on the board
/IOS/LOCK_DET5: J6.4, R18.1; also elsewhere on the board
/IOS/LOCK_DET6: J7.4, R21.1; also elsewhere on the board
/IOS/LOCK_DET7: J8.4, R24.1; also elsewhere on the board
/IOS/LOCK_EN0: R26.1
/IOS/LOCK_EN1: R25.2
/IOS/LOCK_EN2: R28.1
/IOS/LOCK_EN3: R27.2
/IOS/LOCK_EN4: R30.1
/IOS/LOCK_EN5: R29.2
/IOS/LOCK_EN6: R32.1
/IOS/LOCK_EN7: R31.2
/IOS/LOCK_IN0: U1.2 (INA); also elsewhere on the board
/IOS/LOCK_IN1: U1.4 (INB); also elsewhere on the board
/IOS/LOCK_IN2: U2.2 (INA); also elsewhere on the board
/IOS/LOCK_IN3: U2.4 (INB); also elsewhere on the board
/IOS/LOCK_IN4: U3.2 (INA); also elsewhere on the board
/IOS/LOCK_IN5: U3.4 (INB); also elsewhere on the board
/IOS/LOCK_IN6: U4.2 (INA); also elsewhere on the board
/IOS/LOCK_IN7: U4.4 (INB); also elsewhere on the board
GND: C1.2, C2.2, C3.2, C4.2, C5.2, C6.2, C7.2, C8.2, C25.2, C26.2, C27.2, C28.2, C29.2, C30.2, C34.2, C35.2, Q1.2 (S), Q2.2 (S), Q3.2 (S), Q4.2 (S), Q5.2 (S), Q6.2 (S), Q7.2 (S), Q8.2 (S), R2.2, R3.2, R5.2, R6.2, R8.2, R9.2, R11.2, R12.2, R14.2, R15.2, R17.2, R18.2, R20.2, R21.2, R23.2, R24.2, U1.3 (GND), U2.3 (GND), U3.3 (GND), U4.3 (GND); also elsewhere on the board
unnamed: D1.2 (A), J1.3, Q1.3 (D)
unnamed: D2.2 (A), J2.3, Q2.3 (D)
unnamed: D3.2 (A), J3.3, Q3.3 (D)
unnamed: D4.2 (A), J4.3, Q4.3 (D)
unnamed: D5.2 (A), J5.3, Q5.3 (D)
unnamed: D6.2 (A), J6.3, Q6.3 (D)
unnamed: D7.2 (A), J7.3, Q7.3 (D)
unnamed: D8.2 (A), J8.3, Q8.3 (D)
unnamed: Q1.1 (G), R1.1, R2.1
unnamed: Q2.1 (G), R4.1, R5.1
unnamed: Q3.1 (G), R7.1, R8.1
unnamed: Q4.1 (G), R10.1, R11.1
unnamed: Q5.1 (G), R13.1, R14.1
unnamed: Q6.1 (G), R16.1, R17.1
unnamed: Q7.1 (G), R19.1, R20.1
unnamed: Q8.1 (G), R22.1, R23.1
unnamed: R25.1, U1.1 (ENA)
unnamed: R26.2, U1.8 (ENB)
unnamed: R27.1, U2.1 (ENA)
unnamed: R28.2, U2.8 (ENB)
unnamed: R29.1, U3.1 (ENA)
unnamed: R30.2, U3.8 (ENB)
unnamed: R31.1, U4.1 (ENA)
unnamed: R32.2, U4.8 (ENB)

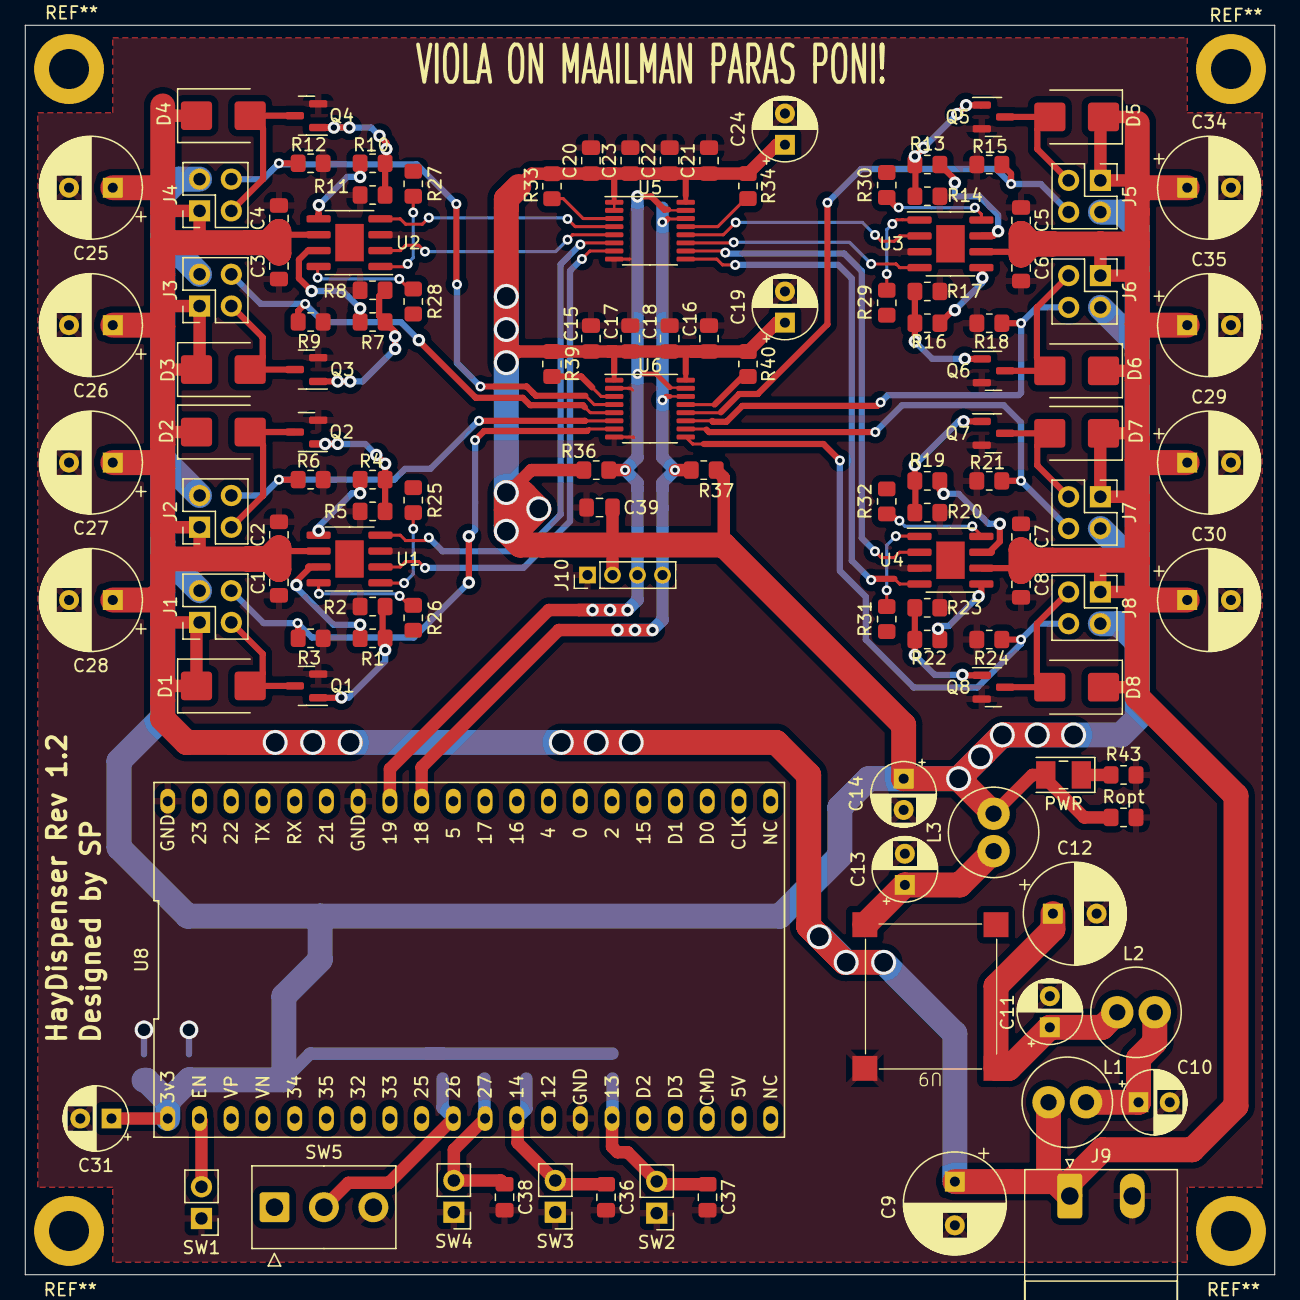
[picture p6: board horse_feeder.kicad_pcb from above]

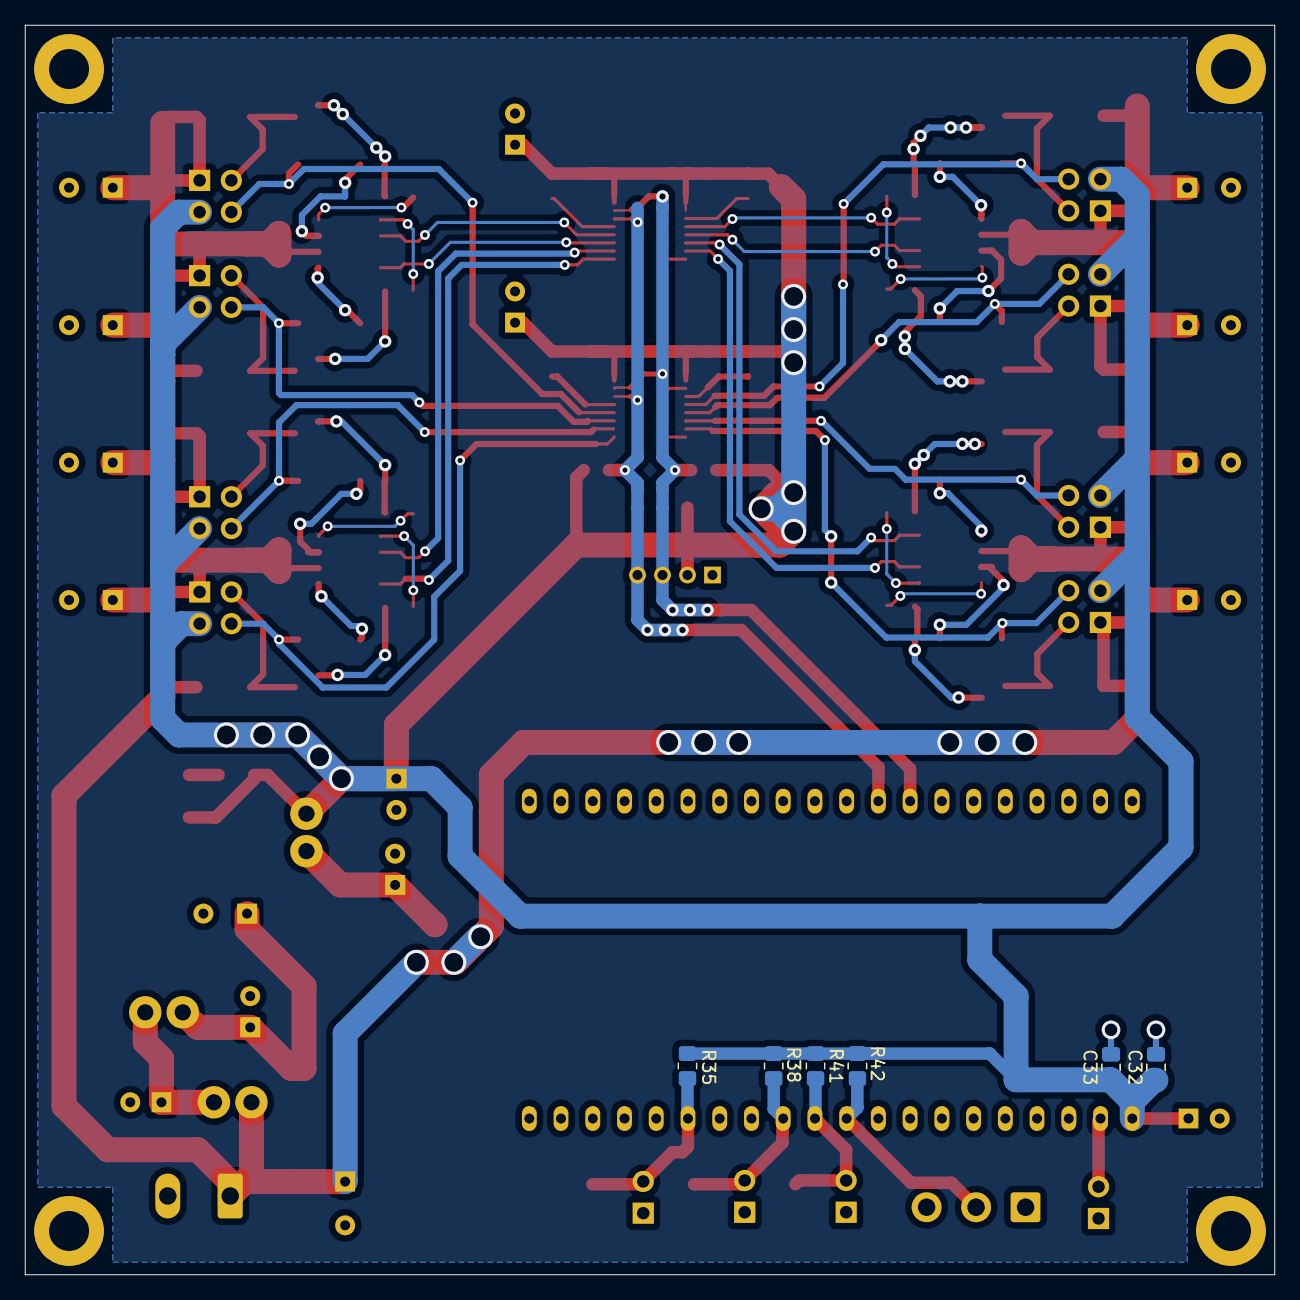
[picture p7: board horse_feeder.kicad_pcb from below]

Board: 2 copper layers, 100.0 x 100.0 mm, 126 parts (6 on the bottom side), 66 nets.

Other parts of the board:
PWR: LED; LED_PLCC-2_3x2mm_KA
Ropt: 330; R_0805_2012Metric_Pad1.20x1.40mm_HandSolder

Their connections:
+3V3: PWR.2 (A), Ropt.1; also elsewhere on the board
GND: Ropt.2; also elsewhere on the board
unnamed 50: PWR.1 (K); also elsewhere on the board

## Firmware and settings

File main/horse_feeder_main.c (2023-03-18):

#include <stdio.h>
#include <string.h>
#include <stdlib.h>
#include <time.h>
#include <sys/time.h>
#include <inttypes.h>
#define LOG_LOCAL_LEVEL ESP_LOG_DEBUG
#include "esp_log.h"
#include "wifi_connect.h"
#include "freertos/FreeRTOS.h"
#include "freertos/task.h"
#include <driver/i2c.h>
#include "timer_handler.h"
#include "ntp_client.h"
#include "gpio_funcs.h"
#include "AIP31068L.h"
#include "wifi_logger.h"

#define LCD_ADDR 0x3e
#define SDA_PIN  19
#define SCL_PIN  18
#define LCD_COLS 16 
#define LCD_ROWS 2
#define NUM_LOCKS 6 // Number of locks in dispenser array
#define STRLEN 8 // Length of one time stamp string, not counting the null byte
#define LOCK_MS 500 // Time to pulse the lock in milliseconds

void LCD_updater(void* param);
void pulseLock(void* param);
void updateAlarm(void* param);
void updateScreenIdxLeft(void* param);
void updateScreenIdxRight(void* param);
//void writeIdxToFlash(void* param);
// Global definition for timer semaphore
SemaphoreHandle_t s_timer_semaphore;
// Global definition for timer update queue (used for sending next alarm value between tasks)
QueueHandle_t update_queue;
// Global definition for screen update queue (used for sending screen idx and mode between tasks)
QueueHandle_t screen_queue;

//QueueHandle_t DPD_event_queue;
//Global definition for button pin interrupt variables:
volatile uint32_t lnum_edges=0;
volatile uint32_t rnum_edges=0;
volatile uint32_t cnum_edges=0;
volatile uint32_t lstate=0;
volatile uint32_t rstate=0;
volatile uint32_t cstate=0;
volatile uint32_t ldebounce_tick=0;
volatile uint32_t rdebounce_tick=0;
volatile uint32_t cdebounce_tick=0;

portMUX_TYPE lmux=portMUX_INITIALIZER_UNLOCKED;
portMUX_TYPE rmux=portMUX_INITIALIZER_UNLOCKED;
portMUX_TYPE cmux=portMUX_INITIALIZER_UNLOCKED;
portMUX_TYPE screen_mux=portMUX_INITIALIZER_UNLOCKED;

static const char* TAG="MAIN";
static const char* TAG_LOCK="PulseLock";
static const char* TAG_ALARM="UpdateAlarm";


int set_tz(const char* targ_tz){
  int ret=setenv("TZ", targ_tz, 1);
  if (ret != 0) {
    ESP_LOGW(TAG, "Error setting TZ variable to %s! Time output will be wrong!!", targ_tz);
    return -1;
  }
  else {
    ESP_LOGI(TAG, "Time zone set to %s.", targ_tz);
    tzset(); // Set timezone from TZ env. variable
    return 0;
  }
}

int init_horse_feeder(void) {
  // TZ variable for Finland
  const char* targ_tz="EET-2EEST,M3.5.0/3,M10.5.0/4";
  // Check first if timezone is set
  char* env_tz=getenv("TZ");
  // If not, try to set
  if (env_tz == NULL) {    
    return set_tz(targ_tz);
  }
  // If it was set, check whether it was correct
  else {
    ESP_LOGI(TAG, "Time zone was %s", env_tz);
    if (strcmp(env_tz, targ_tz)==0) {
      return 0; 
    }
    else { // If not, try to set to correct one
      return set_tz(targ_tz);
    }
  }
}

void init_LCD() {
  ESP_LOGI(TAG, "Starting up LCD");
  //LCD_quick_init(LCD_ADDR, SDA_PIN, SCL_PIN, LCD_COLS, LCD_ROWS);
  struct LCD_config lcd_conf;
  lcd_conf.rows=LCD_ROWS;
  lcd_conf.cols=LCD_COLS;
  lcd_conf.bitmode_flag=1;
  lcd_conf.two_line_flag=1;
  lcd_conf.display_flag=0;
  lcd_conf.pixel_flag=1;
  lcd_conf.cursor_flag=0;
  lcd_conf.blink_flag=0;
  lcd_conf.entrymode_flag=1;
  lcd_conf.shiftmode_flag=0;

  LCD_init(LCD_ADDR, SDA_PIN, SCL_PIN, &lcd_conf);
  LCD_clearScreen();
  LCD_home();
  LCD_writeStr("HorseFeeder 3000");
  LCD_setCursor(0, 1);
  LCD_writeStr("Initializing ...");
}

void app_main(void)
{
  // The parameter to strptime must given as hour (0-23) and minute (0-59)
  char* times[NUM_LOCKS] = {"21:00:00", "00:00:00", "03:00:00", "06:00:00", "09:00:00", "12:00:00"};
  // Table mapping lock indices to GPIO pin numbers
  char buf[6] = { 0 };
  int init_stat=init_horse_feeder();
  if (init_stat != 0) {
    ESP_LOGW(TAG, "Initialization failed!");
  }
#ifdef CONFIG_LCD_ENABLED
  ESP_LOGI(TAG, "LCD configured through menuconfig! Initializing LCD.");
  init_LCD();
#endif
  int wifi_conn_stat=0;
  ESP_LOGI(TAG, "Initializing WiFi");
  //wifi_conn_stat=conn_wifi();
  start_wifi_logger();
  if (wifi_conn_stat != 0) {
    ESP_LOGW(TAG, "Connection failed!");
    ESP_LOGI(TAG, "Restarting in 5 seconds ...");
    vTaskDelay(pdMS_TO_TICKS(5000));
    esp_restart();
  }   
  else {
    esp_log_level_set(TAG_LOCK, ESP_LOG_DEBUG);
    esp_log_level_set(TAG, ESP_LOG_DEBUG);
    ESP_LOGI(TAG, "Connected to WiFi");
    ESP_LOGI(TAG, "Getting current time");
    time_t currtime = get_time();
    ESP_LOGI(TAG, "Setting system time to %s", ctime(&currtime));
    struct timeval tv;
    memset(&tv, 0, sizeof(tv)); // Initialize
    tv.tv_sec=currtime;
    settimeofday(&tv, NULL);

    time_t* arr = NULL;
#ifdef CONFIG_FEEDER_TESTMODE
    arr = malloc(sizeof(time_t) * (NUM_LOCKS+1));
    memset(arr, 0, (NUM_LOCKS+1)*sizeof(time_t));
    for (int i = 0; i < NUM_LOCKS; i++) {
      arr[i] = currtime + (i+1)*CONFIG_TESTMODE_INTERVAL;
    }
#else
    arr=timeFromString(times,sizeof(times)/sizeof(times[0]));
    time_t* arr_cp = NULL;
    arr_cp = malloc(sizeof(time_t) * (NUM_LOCKS+1));
    memset(arr_cp, 0, (NUM_LOCKS+1)*sizeof(time_t));
    arr_cp = timeFromString(times,sizeof(times)/sizeof(times[0]));
#endif
    sort_time(arr, sizeof(times) / sizeof(times[0])); 
#ifndef CONFIG_FEEDER_TESTMODE
    // Try obtain the current lock index corresponding to the index of the original time array
    int lock_idx=0;
    for (int i=0;i<NUM_LOCKS+1;i++) {
      ESP_LOGD(TAG, "Index %d", i);
      ESP_LOGD(TAG, "arr   : %ld", *(arr+i));
      ESP_LOGD(TAG, "arr_cp: %ld", *(arr_cp+i));
      if (*(arr) == *(arr_cp+i)) {
        lock_idx=i;
        break;
      }
    }
    ESP_LOGD(TAG, "The lock to be pulsed is: %d", lock_idx);
    free(arr_cp);
#endif
    //  start task to update time on LCD
#ifdef CONFIG_LCD_ENABLED
      LCD_home();
      LCD_clearScreen();
      LCD_writeStr("PonyFeeder 3000");
      LCD_setCursor(0, 1);
      if (strftime(buf, 6, "%H:%M", localtime(&currtime))!=0) {
        LCD_writeStr("TIME: ");
        LCD_setCursor(6, 1);
        LCD_writeStr(buf);
    }
      // Create array of strings for displaying the alarm times
      char** time_arr = pvPortMalloc(NUM_LOCKS * sizeof(char*));
      for (uint8_t i = 0; i < NUM_LOCKS; i++) {
        time_arr[i] = pvPortMalloc((STRLEN+1)*sizeof(char));
        if (strcpy(time_arr[i], times[i]) != NULL) {
          ESP_LOGD(TAG,"Succesfully dynamically allocated. Array element at idx %d is %s", i, time_arr[i]);
        }
      }
#ifdef CONFIG_BUTTONS_ENABLED
      int* screen_idx = pvPortMalloc(sizeof(int));
      *screen_idx=0;
      screen_queue = xQueueCreate(4, sizeof(int));
      if (screen_queue == NULL) {
        ESP_LOGW(TAG, "Queue creation failed, restarting in 5 s...");
        vTaskDelay(pdMS_TO_TICKS(5000));
        esp_restart();
      }
      // Tasks to update screen index (for chaging the view)
      xTaskCreate(&updateScreenIdxLeft, "updateScreenIdxLeft", 2048, screen_idx, 5, NULL);
      xTaskCreate(&updateScreenIdxRight, "updateScreenIdxRight", 2048, screen_idx, 5, NULL);
#endif
      // Create LCD updater task
      xTaskCreate(&LCD_updater, "LCD_updater", 2048, time_arr, 5, NULL);
#endif
    
    // Time semaphore and update queue
    s_timer_semaphore = xSemaphoreCreateBinary();
    update_queue = xQueueCreate(4, sizeof(time_t));
    if (s_timer_semaphore == NULL) {
      ESP_LOGW(TAG, "Semaphore creation failed, restarting in 5 s...");
      vTaskDelay(pdMS_TO_TICKS(5000));
      esp_restart();
    }
    if (update_queue == NULL) {
      ESP_LOGW(TAG, "Queue creation failed, restarting in 5 s...");
      vTaskDelay(pdMS_TO_TICKS(5000));
      esp_restart();
    }
    // Init timers
    time_t now = time(NULL);
    time_t diff = *arr - now;
    if (diff > 0) {
      ini_timer(0,0, diff);
    }
    else {
      ESP_LOGW(TAG, "Time diff was negative! (%ld seconds)", diff);
    }
    // Init lock pins
    if (lock_pin_init() != 0) {
      ESP_LOGW(TAG, "Lock GPIO init failed, invalid args!");
    }
    // Init buttons
#ifdef CONFIG_BUTTONS_ENABLED
    if (button_pin_init() != 0) {
      ESP_LOGW(TAG, "Button GPIO init failed, invalid args!");
    }
#endif
    // Create tasks to run in background
    xTaskCreate(&pulseLock , "pulseLock", 2048, arr, 5, NULL);
    xTaskCreate(&updateAlarm, "updateAlarm", 2048, NULL, 5, NULL);
  }
}

void updateAlarm(void* param) {
  time_t val = 0;
  for (;;) {
    xQueueReceive(update_queue, &val, portMAX_DELAY);
    if (val > 0) {
      ESP_LOGD(TAG_ALARM, "Setting timer to %ld seconds", val);
      ESP_ERROR_CHECK(timer_set_counter_value(0,0,0));
      ESP_ERROR_CHECK(timer_set_alarm_value(0,0, ((uint64_t) val)*((uint64_t)TIMER_SCALE)));
      ESP_ERROR_CHECK(timer_set_alarm(0,0,1));
    }
    else {
      ESP_LOGW(TAG_ALARM,"Invalid time value for alarm: %ld seconds!!", val);
    }
  }
}

void updateScreenIdxLeft(void* param) {
  int* screen_idx = (int *) param;
  int curr_state=0;
  int num_edges=0;
  int last_state=0;
  int idx=0;
  int debounce_time=0;
  for (;;) {
    // Ensure that ISR doesn't write to variables
    portENTER_CRITICAL(&lmux);
    // Read the last status from button
    num_edges=lnum_edges;
    debounce_time=ldebounce_tick;
    last_state=lstate;
    portEXIT_CRITICAL(&lmux);
    // Read the current state of the button
    curr_state=gpio_get_level(LEFT_PIN);
    // Debounce switch in software
    if ((num_edges != 0) && (curr_state==last_state) && \
        ((xTaskGetTickCount() - debounce_time) > pdMS_TO_TICKS(DEBOUNCE_MS))) {
      (*screen_idx)--;
    if (*screen_idx<0) {
        *screen_idx=6;
      }
      ESP_LOGD(TAG, "Screen idx is now: %d", *screen_idx);
      idx=*screen_idx;
      if (xQueueSend(screen_queue, (void *) &idx, pdMS_TO_TICKS(100) ) != pdPASS) {
        ESP_LOGW(TAG, "Failed to update screen_idx");
      }
      // Reset edge counter
      portENTER_CRITICAL(&lmux);
      lnum_edges=0;
      portEXIT_CRITICAL(&lmux);
      vTaskDelay(pdMS_TO_TICKS(10));
    } 
    else {
      vTaskDelay(pdMS_TO_TICKS(10));
    }
  }
}

void updateScreenIdxRight(void* param) {
  int* screen_idx= (int*) param;
  int curr_state=0;
  int num_edges=0;
  int last_state=0;
  int debounce_time=0;
  int idx=0;
  for (;;) {
    // Ensure that ISR doesn't write to variables
    portENTER_CRITICAL(&rmux);
    // Read the last status from button
    num_edges=rnum_edges;
    debounce_time=rdebounce_tick;
    last_state=rstate;
    portEXIT_CRITICAL(&rmux);
    // Read the current state of the button
    curr_state=gpio_get_level(LEFT_PIN);
    // Debounce switch in software
    if ((num_edges != 0) && (curr_state==last_state) && ((xTaskGetTickCount() - debounce_time) > pdMS_TO_TICKS(DEBOUNCE_MS))) {
      (*screen_idx)++;
      if (*screen_idx>6) {
        (*screen_idx)=0;
      }
      ESP_LOGD(TAG, "Screen idx is now: %d", *screen_idx);
      idx=*screen_idx;
      if (xQueueSend(screen_queue, (void *) &idx, pdMS_TO_TICKS(100) ) != pdPASS) {
        ESP_LOGW(TAG, "Failed to update screen_idx");
      }
      // Reset edge counter
      portENTER_CRITICAL(&rmux);
      rnum_edges=0;
      portEXIT_CRITICAL(&rmux);
      vTaskDelay(pdMS_TO_TICKS(10));
    } 
    else {
      vTaskDelay(pdMS_TO_TICKS(10));
    }
  }
}
  
void pulseLock(void* param) {
  /*
    This function is responsible for pulsing the lock when the hardware
    timer alarm is triggered. Pulsing the lock will dispense one portion
    of hay. If the power goes out for an undetermined amount of time,
    all locks with time stamps smaller than the current time should also
    be pulsed.
    
    the strategy to determine
    which lock will be pulsed will be as follows:

    1. Parameter time_arr is to given as non-sorted version of the array
    2. Sort the array, first element should be closest to the next lock release
    3. Associate lock_idx = 0 with this time, this assures 
  */
  time_t* t_arr = (time_t*) param;
  time_t now = 0, diff = 0, offs=0;
  int lock_idx = 0;
  int idxToPin[NUM_LOCKS] = { LOCK_GPIO_0, LOCK_GPIO_1, LOCK_GPIO_2, LOCK_GPIO_3, LOCK_GPIO_4, LOCK_GPIO_5 };
#ifdef CONFIG_FEEDER_TESTMODE
  offs = CONFIG_TESTMODE_INTERVAL*6;
#else
  offs = 24*3600;
#endif
  for (;;) {
    // Wait until ISR gives semaphore, increment lock_idx counter
    xSemaphoreTake(s_timer_semaphore, portMAX_DELAY);
    ESP_LOGD(TAG_LOCK, "INTERRUPT FROM TIMER");
    ESP_LOGD(TAG_LOCK, "RELEASING LOCK ON GPIO IDX: %d", *(idxToPin+lock_idx));
    gpio_set_level(*(idxToPin+lock_idx), 1); // MOSFET drivers are active high 
    vTaskDelay(pdMS_TO_TICKS(LOCK_MS));
    gpio_set_level(*(idxToPin+lock_idx), 0);
    // Increment lock idx, loop back to zero if over range
    ESP_LOGD(TAG_LOCK, "LOCK IDX WAS: %d, Incrementing.", lock_idx);
    if (lock_idx >= 5) {
      lock_idx=0; 
      ESP_LOGD(TAG_LOCK, "LOCK IDX OVERRANGE, Looping back to zero");
    }
    else {
      lock_idx++;
    }
    ESP_LOGD(TAG_LOCK, "LOCK IDX IS: %d", lock_idx);
    now = time(NULL);
    diff = *(t_arr+lock_idx) - now;
    if (diff > 0) {
      if (xQueueSend(update_queue, (void *) &diff, pdMS_TO_TICKS(100) ) != pdPASS) {
        ESP_LOGW(TAG_LOCK, "FAILED TO UPDATE ALARM!");
      }
    } 
    else {
      ESP_LOGD(TAG_LOCK, "Time diff was negative! (%ld seconds)", diff);
      ESP_LOGD(TAG_LOCK, "Increasing time_arr values %ld seconds.", offs);
      for (uint8_t i = 0; i < NUM_LOCKS; i++) {
        *(t_arr+i) += offs;
      }
      sort_time(t_arr, NUM_LOCKS);
      now=time(NULL);
      diff = *(t_arr+lock_idx) - now;
      if (xQueueSend(update_queue, (void *) &diff, pdMS_TO_TICKS(100) ) != pdPASS) {
        ESP_LOGW(TAG_LOCK, "FAILED TO UPDATE ALARM!");
      }
    }
  }
}

void LCD_updater(void* param) {
/*
   This task should run every 60 seconds or so
   to update the time reading on the LCD screen
   TODO: Add a queue/semaphore to be given by ISR.
   Based on that, increment/decrement screen idx
   and display alarm times on the LCD screen.
*/
  char** times= (char **) param;
  for (uint8_t i = 0; i < NUM_LOCKS; i++) {
    ESP_LOGD(TAG,"String at idx %d is %s", i, *(times+i));
  }
  char txtbuf[16];
  int screen_idx=0;
  time_t now;
  struct tm timeinfo;
  TickType_t xLastWakeTime;
  // Calculate ticks until next full minute
  TickType_t xFreq = 0;
  xLastWakeTime = xTaskGetTickCount();
  while (1) {
    // Wait until it's time to update or we receive index from queue
    now=time(NULL);
    xFreq = pdMS_TO_TICKS((60 - (now - (now / 60)*60))*(1000));
    ESP_LOGV(TAG, "Waiting %d milliseconds until next screen refresh", xFreq);
#ifdef CONFIG_BUTTONS_ENABLED
    if (xQueueReceive(screen_queue, &screen_idx, xFreq) == pdFALSE) {
      if (screen_idx == 0) {
        vTaskDelayUntil(&xLastWakeTime, xFreq);
        LCD_clearScreen();
        LCD_setCursor(0,0);
        LCD_writeStr("PonyFeeder 3000");
        LCD_setCursor(0, 1);
        now=time(NULL);
        localtime_r(&now, &timeinfo);
        sprintf(txtbuf, "TIME: %02d:%02d", timeinfo.tm_hour, timeinfo.tm_min);
        LCD_writeStr(txtbuf);
      }
    } 
    // Received something from queue, display alarm times
    else {
      switch (screen_idx) {
        case 0:
          LCD_clearScreen();
          LCD_setCursor(0,0);
          LCD_writeStr("PonyFeeder 3000");
          LCD_setCursor(0, 1);
          now=time(NULL);
          localtime_r(&now, &timeinfo);
          sprintf(txtbuf, "TIME: %02d:%02d", timeinfo.tm_hour, timeinfo.tm_min);
          LCD_writeStr(txtbuf);
          break;
        case 1:
          LCD_clearScreen();
          LCD_setCursor(0,0);
          LCD_writeStr("Alarm time for");
          LCD_setCursor(0,1);
          sprintf(txtbuf, "LOCK1: %s", times[0]);
          LCD_writeStr(txtbuf);
          break;
        case 2:
          LCD_clearScreen();
          LCD_setCursor(0,0);
          LCD_writeStr("Alarm time for");
          LCD_setCursor(0,1);
          sprintf(txtbuf, "LOCK2: %s", times[1]);
          LCD_writeStr(txtbuf);
          break;
        case 3:
          LCD_clearScreen();
          LCD_setCursor(0,0);
          LCD_writeStr("Alarm time for");
          LCD_setCursor(0,1);
          sprintf(txtbuf, "LOCK3: %s", times[2]);
          LCD_writeStr(txtbuf);
          break;
        case 4:
          LCD_clearScreen();
          LCD_setCursor(0,0);
          LCD_writeStr("Alarm time for");
          LCD_setCursor(0,1);
          sprintf(txtbuf, "LOCK4: %s", times[3]);
          LCD_writeStr(txtbuf);
          break;
        case 5:
          LCD_clearScreen();
          LCD_setCursor(0,0);
          LCD_writeStr("Alarm time for");
          LCD_setCursor(0,1);
          sprintf(txtbuf, "LOCK5: %s", times[4]);
          LCD_writeStr(txtbuf);
          break;
        case 6:
          LCD_clearScreen();
          LCD_setCursor(0,0);
          LCD_writeStr("Alarm time for");
          LCD_setCursor(0,1);
          sprintf(txtbuf, "LOCK6: %s", times[5]);
          LCD_writeStr(txtbuf);
          break;
        default:
          screen_idx=0;
          break;
      } 
    }
#else
    vTaskDelayUntil(&xLastWakeTime, xFreq);
    LCD_clearScreen();
    LCD_setCursor(0,0);
    LCD_writeStr("PonyFeeder 3000");
    LCD_setCursor(0, 1);
    now=time(NULL);
    localtime_r(&now, &timeinfo);
    sprintf(txtbuf, "TIME: %02d:%02d", timeinfo.tm_hour, timeinfo.tm_min);
    LCD_writeStr(txtbuf);
#endif
  }
}

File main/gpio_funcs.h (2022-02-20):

#ifndef GPIO_FUNCS_H
#define GPIO_FUNCS_H

#include "freertos/FreeRTOS.h"
#include "freertos/task.h"
#include "freertos/queue.h"
#include "driver/gpio.h"

// GPIO pins controlling the locks. Lock 0 is the bottom-most lock
#define LOCK_GPIO_0 23
#define LOCK_GPIO_1 22
#define LOCK_GPIO_2 4
#define LOCK_GPIO_3 21
#define LOCK_GPIO_4 32
#define LOCK_GPIO_5 33
// Bit mask for output pins (is there a more reasonable way of doing this definition?)
#define GPIO_OUTPUT_PIN_SEL ((1ULL << LOCK_GPIO_0) | (1ULL << LOCK_GPIO_1) \
    | (1ULL << LOCK_GPIO_2) | (1ULL << LOCK_GPIO_3) | (1ULL << LOCK_GPIO_4) \
    | (1ULL << LOCK_GPIO_5))

#define DPD_GPIO 13 // Power down detection pin
#define DPD_GPIO_SEL (1ULL << DPD_GPIO) // Bit mask for DPD pin

#define LEFT_PIN 34
#define RIGHT_PIN 35
#define CENTER_PIN 25

// Time used for debouncing (in milliseconds)
#define DEBOUNCE_MS 200

#define BUTTON_PIN_SEL ((1ULL << LEFT_PIN) | (1ULL << RIGHT_PIN) | (1ULL << CENTER_PIN))

void IRAM_ATTR write_lock_idx_isr(void* arg);
void IRAM_ATTR button_left_interrupt(void* arg);
void IRAM_ATTR button_right_interrupt(void* arg);
void IRAM_ATTR button_center_interrupt(void* arg);

uint8_t lock_pin_init();
uint8_t button_pin_init();

uint8_t dpd_pin_init(int* lock_idx);

extern QueueHandle_t DPD_event_queue;
extern portMUX_TYPE lmux;
extern portMUX_TYPE rmux;
extern portMUX_TYPE cmux;
extern volatile uint32_t lnum_edges;
extern volatile uint32_t rnum_edges;
extern volatile uint32_t cnum_edges;
extern volatile uint32_t lstate;
extern volatile uint32_t rstate;
extern volatile uint32_t cstate;
extern volatile uint32_t ldebounce_tick;
extern volatile uint32_t rdebounce_tick;
extern volatile uint32_t cdebounce_tick;

#endif

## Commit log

2021-09-12 Printing local time to LCD works
2021-09-12 Add schematic
    [horse_feeder.kicad_pcb, horse_feeder.sch]
2021-09-14 Fix bug with localtime()
    [horse_feeder_main.c]
2021-09-14 Fix erratic behaviour with LCD time
    [horse_feeder_main.c]
2021-09-17 Timer works
2021-09-20 Moved timer related stuff to own file
2021-09-20 Timer retriggering works poorly
2021-09-23 Timer works, need to reshuffle times after final value
2021-09-25 Renamed timer to timer_handler
2021-09-25 GPIO power down interrupt works
2021-09-25 Update schematic
    [horse_feeder.sch]
2021-09-25 Fix timer alarm value input
    [horse_feeder_main.c]
2021-10-02 Switch debouncing in software works
2021-10-03 Improved handling of left/right buttons
2022-01-16 Modified schematic and PCB
    [IOs.sch, horse_feeder.sch, mcu.sch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]
2022-01-16 Added pullups for I2C
    [IOs.sch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]
2022-02-20 Test with produced PCB
2023-03-18 KiCAD latest version now up to date
    [IOs.kicad_sch, horse_feeder.kicad_pcb, horse_feeder.kicad_sch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]
2023-07-03 Update PCB with IO expander
    [IOs.kicad_sch, horse_feeder.kicad_pcb, horse_feeder.kicad_sch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]
2023-07-04 Fix remaining DRC + ERC, ready for manufacturing
    [IOs.kicad_sch, horse_feeder.kicad_pcb, mcu.kicad_sch]
2023-07-04 PCB order
    [horse_feeder-B_Cu.gbl, horse_feeder-B_Mask.gbs, horse_feeder-B_Paste.gbp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]
